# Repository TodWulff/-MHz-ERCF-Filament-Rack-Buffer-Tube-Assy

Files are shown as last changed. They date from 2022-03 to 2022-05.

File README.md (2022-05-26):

# ~MHz ERCF Filament Rack/Buffer Tube Array

## Per user request, I went ahead and created STLs from gcode generated from the project file.  Hopefully these will work with little to no issue.  Let me know, please.  TIA

## (see bottom section for details on a recent mod to add filament guide 'ramps' to ensure filament doesn't miss the buffer wheel when the buffer empties)

Being inspired by having drama with the ERCP Filament Buffer assemblies, coupled with watching a [RMU video on Chris Riley's youtube channel](https://youtu.be/tYeIUff-35k?t=219), I decided to undertake the endeavor of fabricobbling a KISS buffer solution that didn't rely on multiple loops of filament.  With that, I present the following to y'all for your consideration of how one gent went about tackling same.  This solution provides ~1750mm of filament buffer for each filament channel (12 channel solution pictured here).

~MHz ERCF Filament Rack/Buffer Tube Assy

The 'buffer tubes' are [Betaduct 75mm*25mm solid wall raceways](https://github.com/TodWulff/-MHz-ERCF-Filament-Rack-Buffer-Tube-Assy/blob/main/PN_09240000Y.pdf).  I got a set of [8ea 2m long pieces for roughly $120 from Newark](https://www.newark.com/betaduct/09240000y/solid-wall-duct-pvc-blk-75x25mm/dp/24AJ3284?ICID=I-RP-STM7REC-1).  The PVC flavor is what I bought.  The Noryl flavor is roughly [5x more expensive](https://www.newark.com/betaduct/23473000n/solid-wall-duct-noryl-blk-75x25mm/dp/24AJ3781?ICID=I-RP-STM7REC-1) - be careful.  The buffer tubes pictured above are cut to 36" in length.  
- [Engineering Drawing](https://github.com/TodWulff/-MHz-ERCF-Filament-Rack-Buffer-Tube-Assy/blob/main/betaduct_pvc_solid_wall_75_x_25_drawing.pdf)  
- [Step File from Cablecraft (OEM}](https://github.com/TodWulff/-MHz-ERCF-Filament-Rack-Buffer-Tube-Assy/blob/main/03-1709.STEP)

I cobbled the [endcap assy's together in PrusaSlicer](https://github.com/TodWulff/-MHz-ERCF-Filament-Rack-Buffer-Tube-Assy/blob/main/MHzBufferTubeEndCapAssy.3mf) (/me != 3D CAD skills).

Endcap Platter

Endcap Sliced

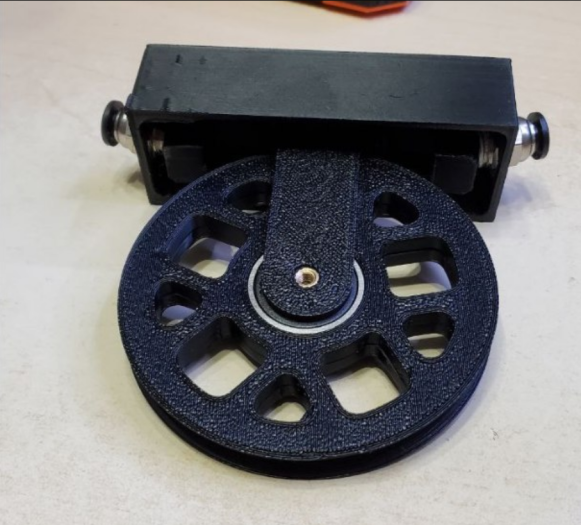
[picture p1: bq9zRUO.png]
~MHz Filament Buffer Tube Endcap Assy


Each assembled Endcap needs 2ea [PC4-M10](https://www.amazon.com/ExcelFu-Straight-Pneumatic-Connector-Long-Distance/dp/B07P2XRCC1), 1ea [608RS Bearing](https://www.amazon.com/gp/product/B073ST742Z), 1ea M3 Heat insert, 4ea M3x10 screws (to attach the hanger halves to the lid) and 1ea M3x16 screw for the bearing axis - to tie the stack of parts together.

The bowden comb is an extra that I added to the model - ensures that one has more than enough if multiple end caps are printed.  Also, on the ERCPs, using a piece of filament as the axis that the PC4-M10 coupler/holder slides on is a design choice that I find substandard. I ended up using jobber length 1.75mm drill bits - works well...

For the frame, I ordered a set of [10ea 1000mm lengths of 2020](https://www.amazon.com/Montex-Aluminum-Extrusion-European-Standard/dp/B093FDT2QN), in addition to a couple additional pieces I had stock on - used for the bottom anti-tip supports - printed feet/end caps (sharp edges will cut a toe or three off).  The 4 up rights are 1000mm, the lateral pieces are 650-ish mm.

I used a ton of [roll-in M5 t-nuts](https://www.amazon.com/gp/product/B07VHNGBWJ) and 2 sets of these to tie it all together: https://smile.amazon.com/KOOTANS-Bracket-Connection-Aluminum-Profile/dp/B07RPT9X8X , along with a set of these for the top of the verticals: https://smile.amazon.com/Befenybay-Connector-Aluminum-Extrusion-2020s-Black/dp/B092YS1SX3.

The 4 members holding the buffer tubes are just the left overs from lobbing the lateral pieces down to 650mm, trimmed to length to allow ample spacing between the buffers - I may actually squeeze the buffer wings tighter and trim the metal down more - tbd - this was a **finalize-the-design-while-building** evolution.

At the top of each buffer tube, I used this type of bit to plow a hole through on each side (used an extra printed cap as a guide) and then dyked the top of the material away to allow the cap to be slid on/off without having to unscrew anything - makes servicing a breeze.

Buffer Tube - Endcap Interface

M5x8 with roll-ins round it out and hold the tubes to the wings.  The bowden tube I used is here:  https://smile.amazon.com/MUYI-Chemical-Electrical-Medical-Equipment/dp/B019PZ5MY4.  It's 2mm ID but my orbiter v1.5 has plenty of pulling power, so no issues for me, with #4/#5 tophats driven by a NMEA 17 gear stepper (Y axis servo from my E3v2 in the printer graveyard).

Note:  Expect to have to do some post processing - I am printing ABS fast with a 0.9mm nozzle & I needed to enlarge some of the holes with a deburring tool.  Also might want to make the bowden comb's cutouts (the negative volume modifiers) a bit larger - i.e. increase diameter by 0.2mm.  I had to go back and redrill all of them so the bowden tubes would slide in.

~~EDIT:  I've had one instance of the filament coming off the wheel with the initial design - stayed on the sides of the wheel, but the bottom was not riding the wheel radius - I was messing with the filament spools at the time and I think I imputed a twist.?.  However, if it happens again, I will amend the design with a lower hemispherical 'ramp' to prevent same.  Time will tell...~~

EDIT:  I've decided to create and add another [.3mf Prusa Slicer project file to add filament guide ramps](https://github.com/TodWulff/-MHz-ERCF-Filament-Rack-Buffer-Tube-Assy/blob/main/MHzBufferTubeFilamentGuides.3mf) that aid in preventing the filament from coming off of the buffer wheel - hasn't happened again, but could and wanted a robust solution for y'all.  This should address the one-time issue I observed.  The only BOM change is the buffer bearing axle screw - a M3x16 BHCS is now required.  The M3 heat insert now gets installed in one of the guide halves (the one without the screw head recess) and serves to secure the stack (filament guide half, buffer hanger half, buffer with bearing, buffer hanger half, filament guide half (with heat insert)).  Pay attention to the orientation of the filament guides WRT the buffer tube cap, as one side is tapered by design (goes on the cap side of the buffer tube).

Filament Guides Slicer Images:

layout 
sliced

Assembly Images Cap, PC4-M10s, Wheel Hanger, Buffer Wheel, and Filament Guides:

Before/After Filament Guide Assy

Before/After Filament Guide Assy

Post assembly closeup

Post assembly closeup

Completed assembly with guides fitted into the buffer tube (buffer still spins easy enough)

Fitted into the buffer tube

parts stack

Each buffer tube assy will need, 1ea length of buffer tube cut from the betaduct lengths (36" is good), 1ea Cap, 2ea Hanger Halves, 1ea Buffer Wheel, and 1ea of Guide A and Guide B, along with the bearing, 2ea PC4-M10 couplers, and other hardware spoken to above (4+1 screws and 1 M3 heat insert)(.

Endcap Printing takes a while...

Endcap Printing takes a while...

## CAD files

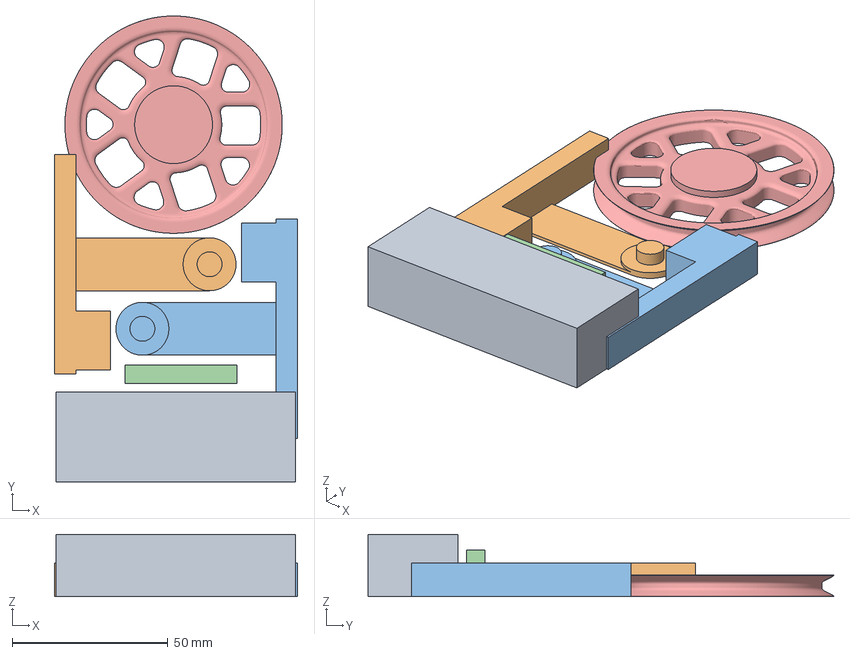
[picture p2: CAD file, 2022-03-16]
MHzBufferTubeEndCapAssy.3mf
78.2 x 149.7 x 20.0 mm
CapAssy
CapHangarAssy x 2
BowdenClip
BufferWheel

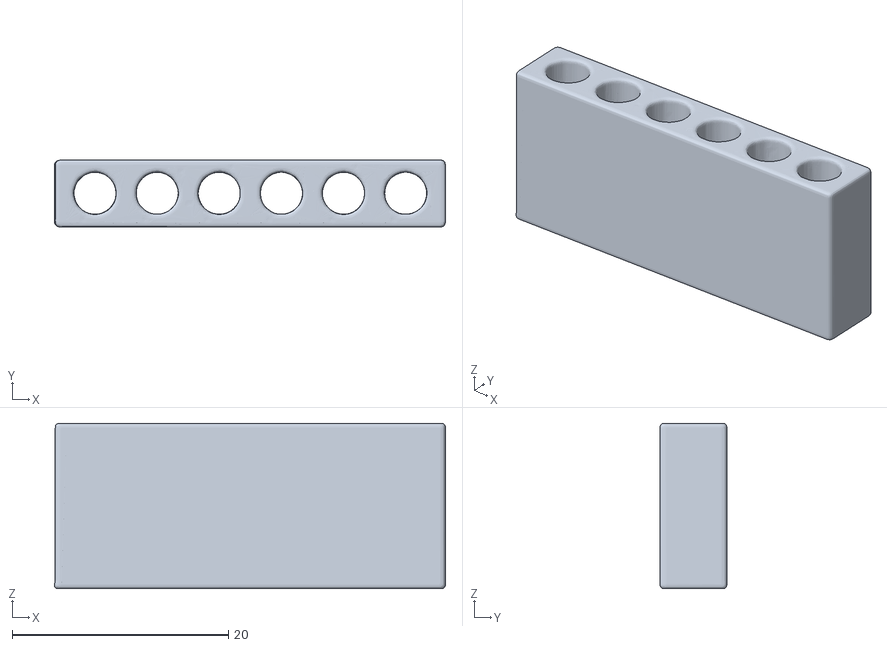
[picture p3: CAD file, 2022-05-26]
MHzBufferTubeEndCapAssySTLs/MHzBufferBowdenComb.stl
36.2 x 6.20 x 15.3

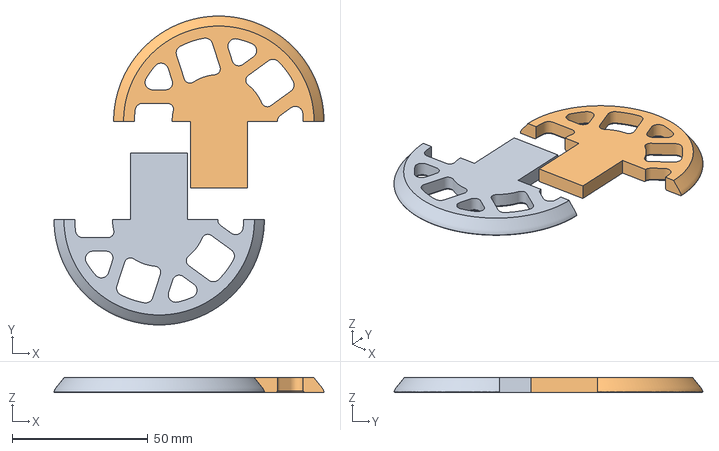
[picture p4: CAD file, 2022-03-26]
MHzBufferTubeFilamentGuides.3mf
99.5 x 113.8 x 5.50 mm
BufferWheelRampA
BufferWheelRampB

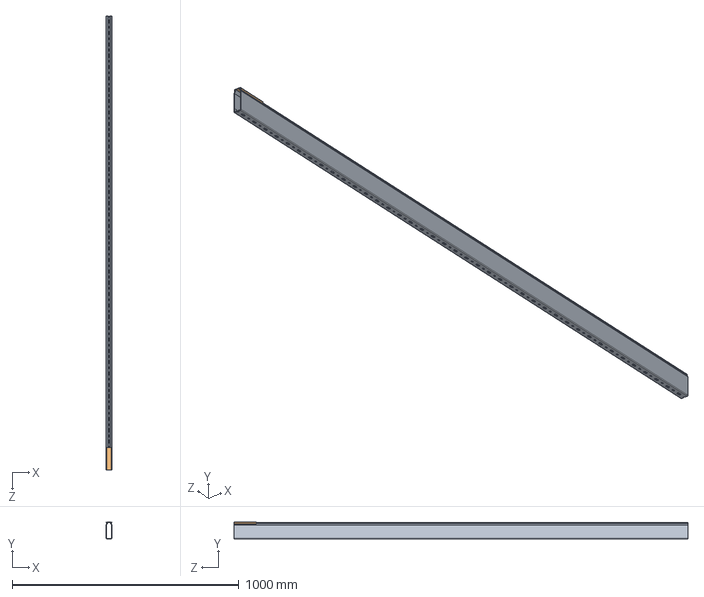
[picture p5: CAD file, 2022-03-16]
03-1709.STEP
25.0 x 73.0 x 2000.0 mm
03-0997_S
03-0498_Lg 100

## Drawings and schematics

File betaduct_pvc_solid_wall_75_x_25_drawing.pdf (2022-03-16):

# Drawing

# Betaduct PVC Solid Wall Trunking H: 75mm x W: 25mm

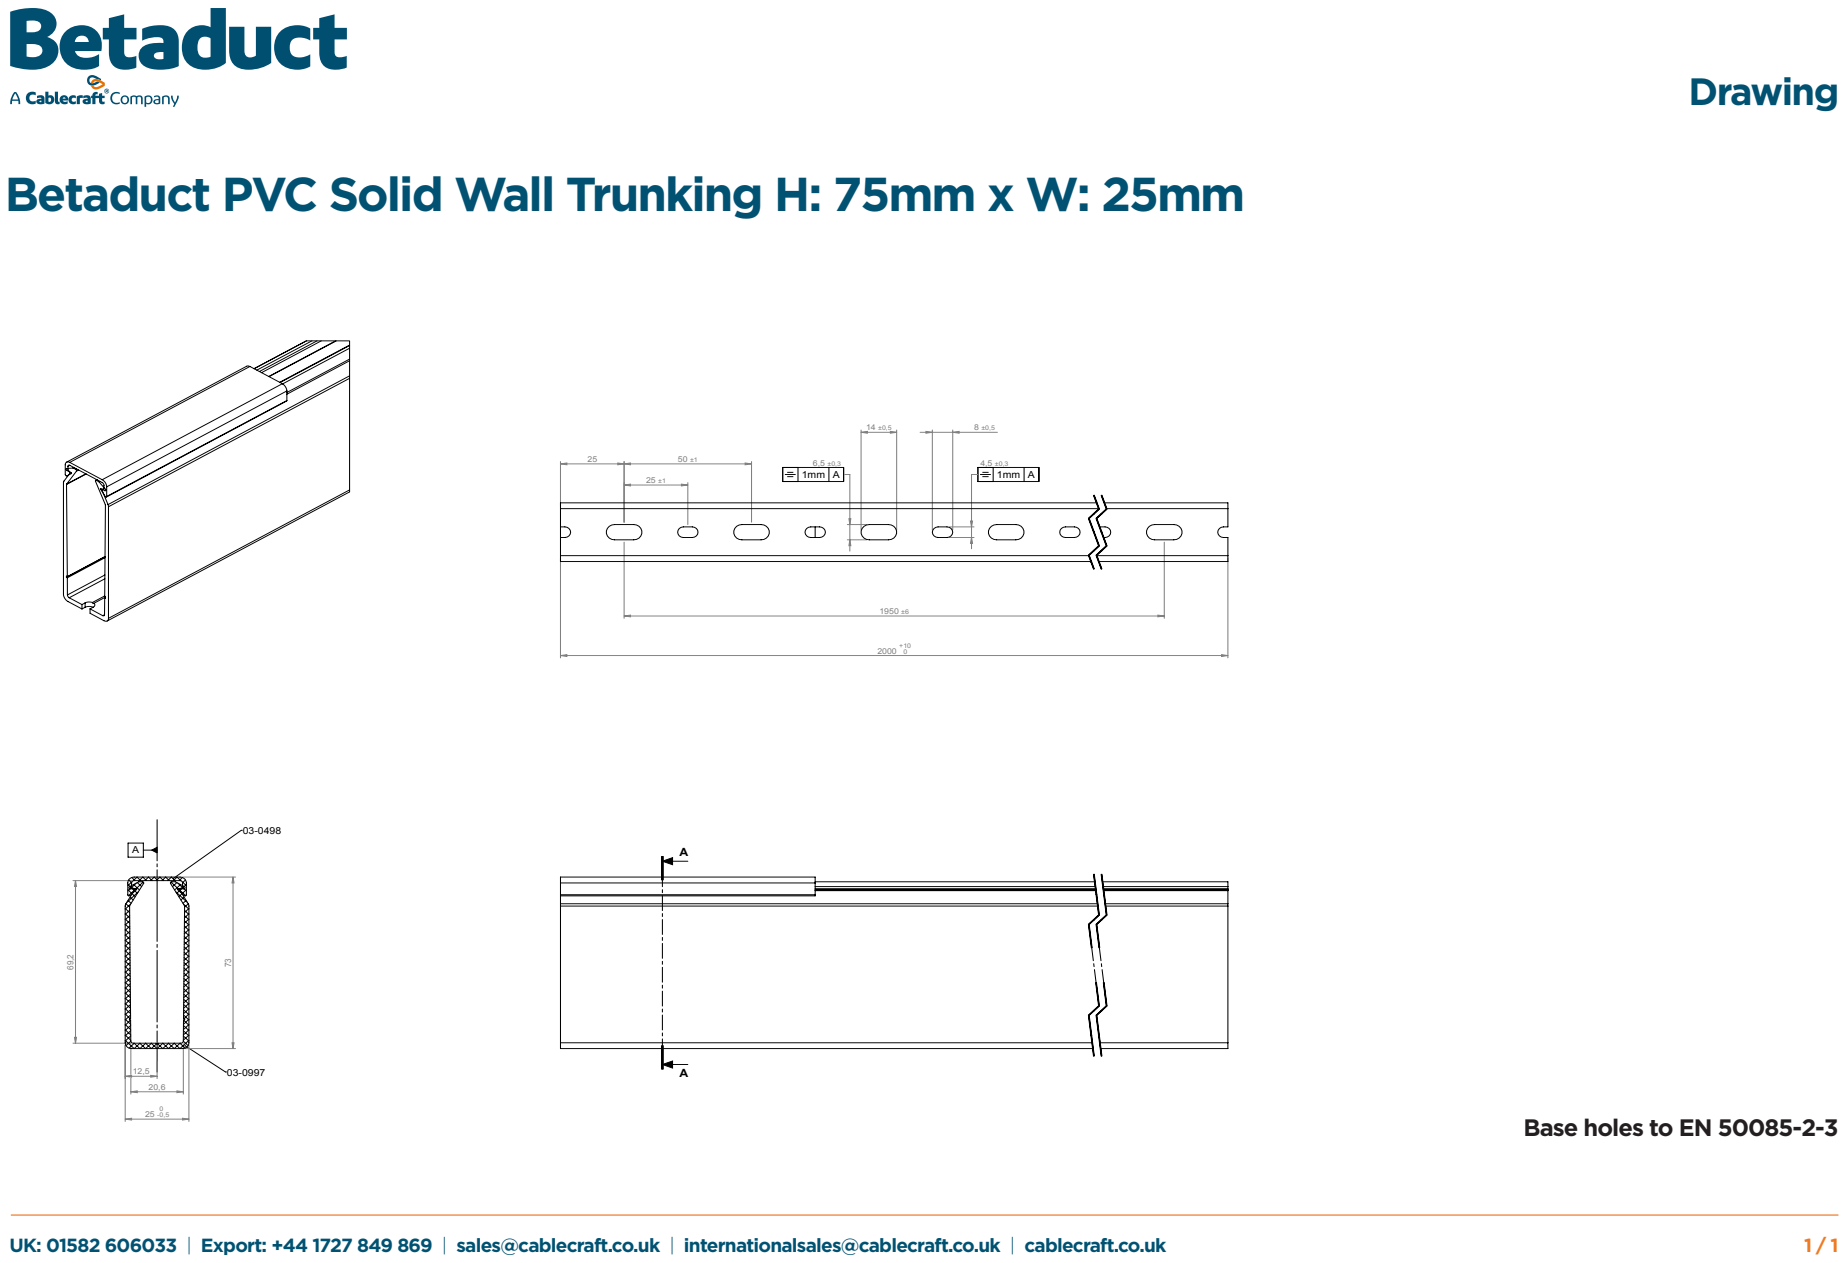
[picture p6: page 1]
UK: 01582 606033 | Export: +44 1727 849 869 | sales@cablecraft.co.uk | internationalsales@cablecraft.co.uk | cablecraft.co.uk; Commentaire :; CODE ART :

Base holes to EN 50085-2-3

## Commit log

2022-03-26 Created Filament Guides
    Added a Prusa Slicer project file for filament guides that fill the void between the buffer wheel and the outer walls of the buffer tubes to prevent filament that may have a twist to it from becoming wrapped around the outside of the buffer wheel.
    [MHzBufferTubeFilamentGuides.3mf]
2022-05-26 Added STLs based on gcode from sliced project files
    [MHzBufferBowdenComb.stl]
